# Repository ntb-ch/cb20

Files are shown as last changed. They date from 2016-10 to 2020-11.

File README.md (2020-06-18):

# cb20
Controller Board with Processor Module Toradex Colibri iMX6

## Documentation
- Hardware and software: https://wiki.ntb.ch/infoportal/embedded_systems/imx6/cb
- Linux on the cb20: https://wiki.ntb.ch/infoportal/software/linux/toradex/start

## FPGA Designs
There are currently three FPGA designs in the repository:
* standard: design with encoder inputs, DAC, PWM outputs and some digital I/O pins
* watchdog: similar to standard design, adds PPWA and watchdog with fewer PWM pins
* mpu9250: similar to standard design, adds SPI interface for the MPU-9250 IMU chip of InvenSense, with fewer PWM channels

## Software
We use the board together with [EEROS Robotics Framework](https://github.com/eeros-project/eeros-framework) and [flink](https://github.com/flink-project).
- Demo application: in this repository under Software/cb20test
- How to use, see [Get Started Using EEROS](https://wiki.eeros.org/getting_started/start)

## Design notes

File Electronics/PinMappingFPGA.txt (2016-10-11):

PIN-Mapping FPGA:

=== IO ===
IO_1:	P1\\
IO_2:	P2\\
IO_3:	N1\\
IO_4:	N2\\
IO_5:	L1\\
IO_6:	L2\\
IO_7:	K1\\
IO_8:	K2\\

=== PWM ===
PWM_1:	A2\\
PWM_2:	B3\\
PWM_3:	A3\\
PWM_4:	B4\\
PWM_5:	A4\\
PWM_6:	B5\\
PWM_7:	A5\\
PWM_8:	A6\\

=== Enable/Ready ===
ENABLE:			G1\\
READY_DRV_1:	G2\\
READY_DRV_2:	F1\\
READY_DRV_3:	F2\\
READY_DRV_4:	D1\\
READY_DRV_5:	D2\\
READY_DRV_6:	C1\\
READY_DRV_7:	C2\\
READY_DRV_8:	B1\\

=== Encoder ===
ENC_A1:	L8\\
ENC_B1:	M8\\
ENC_A2:	T5\\
ENC_B2: R4\\
ENC_A3:	T4\\
ENC_B3:	R3\\
ENC_A4:	T3\\
ENC_B4:	T2\\
ENC_A5:	P6\\
ENC_B5:	P3\\
ENC_A6:	N3\\
ENC_B6: N5\\
ENC_A7: N6\\
ENC_B7:	M6\\
ENC_A8:	M7\\
ENC_B8:	L7\\

=== SPI DAC ===
!CLR:	R5\\
!SYNC:	T6\\
!LDAC:	R6\\
MOSI:	T7\\
SCLK:	R7\\

=== EIM ===
DATA0:	T15\\
DATA1:	P14\\
DATA2:	R14\\
DATA3:	T14\\
DATA4:	R13\\
DATA5:	T13\\
DATA6:	N12\\
DATA7:	R12\\
DATA8:	T12\\
DATA9:	N11\\
DATA10:	P11\\
DATA11:	R11\\
DATA12:	T11\\
DATA13:	R10\\
DATA14:	T10\\
DATA15:	P9\\

ADDRESS0:	J15\\
ADDRESS1:	J16\\
ADDRESS2:	J13\\
ADDRESS3:	J14\\
ADDRESS4:	L13\\
ADDRESS5:	L14\\
ADDRESS6:	N15\\
ADDRESS7:	N16\\
ADDRESS8:	K16\\
ADDRESS9:	K15\\
ADDRESS10:	N14\\
ADDRESS11:	P16\\
ADDRESS12:	P15\\
ADDRESS13:	R16\\
ADDRESS14:	L15\\
ADDRESS15:	L16\\

CS1:		G16\\
CS0:		G15\\
OE:		F13\\
PWE:		F16\\
RDY:		F15\\
DF_WE:		B16\\
RD_WR:		F14\\
WE:		D16\\
BE0:		D15\\
BE1:		C16\\
DF_RE_OE:	C15\\

=== Config ===
DCLK:		H1\\
CONF_DONE:	H14\\
nCONFIG:	H5\\
nSTATUS:	F4\\

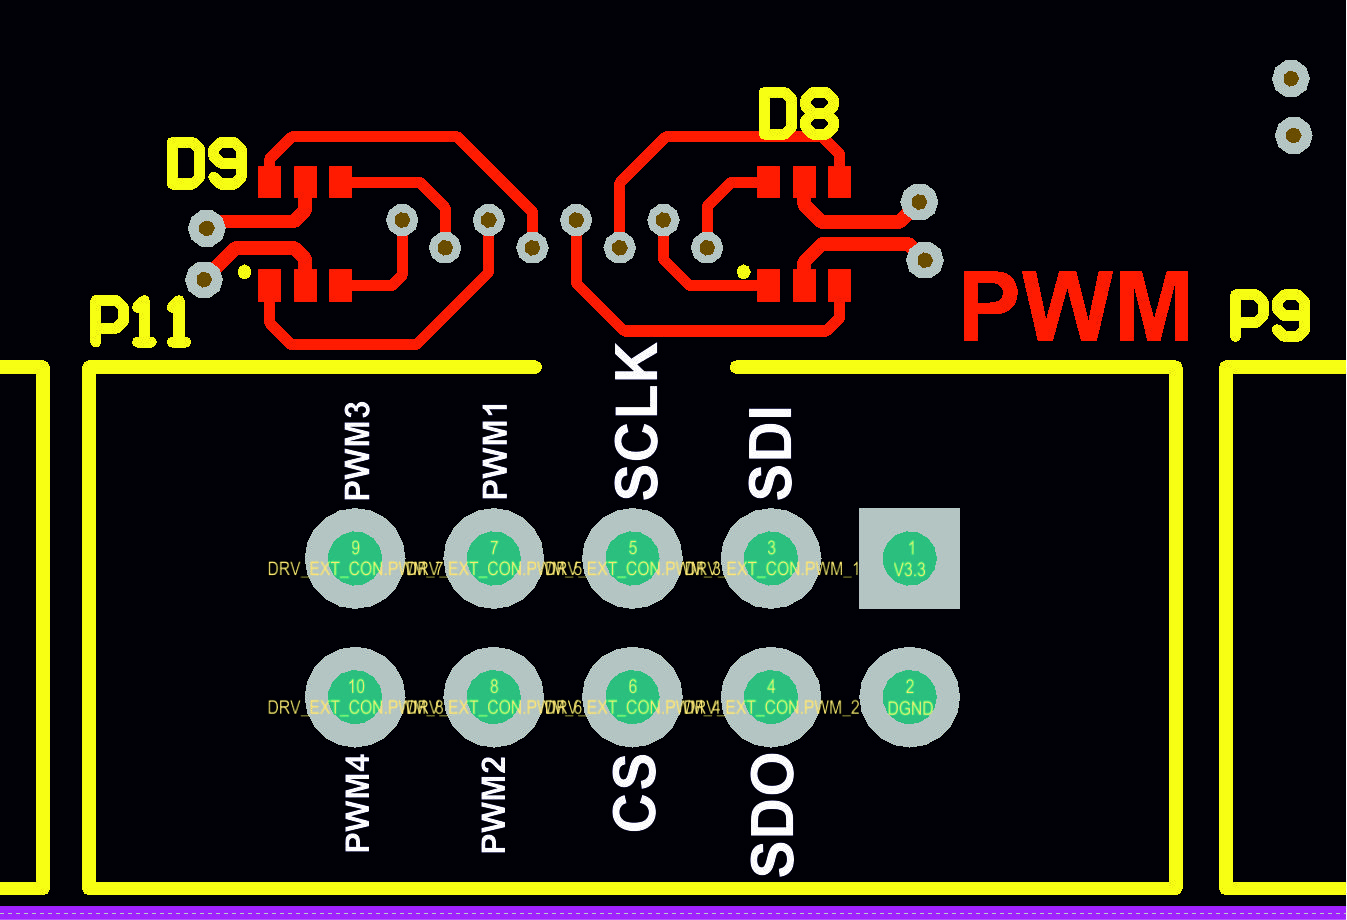
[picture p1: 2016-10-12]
Electronics/Cb20Spi.jpg

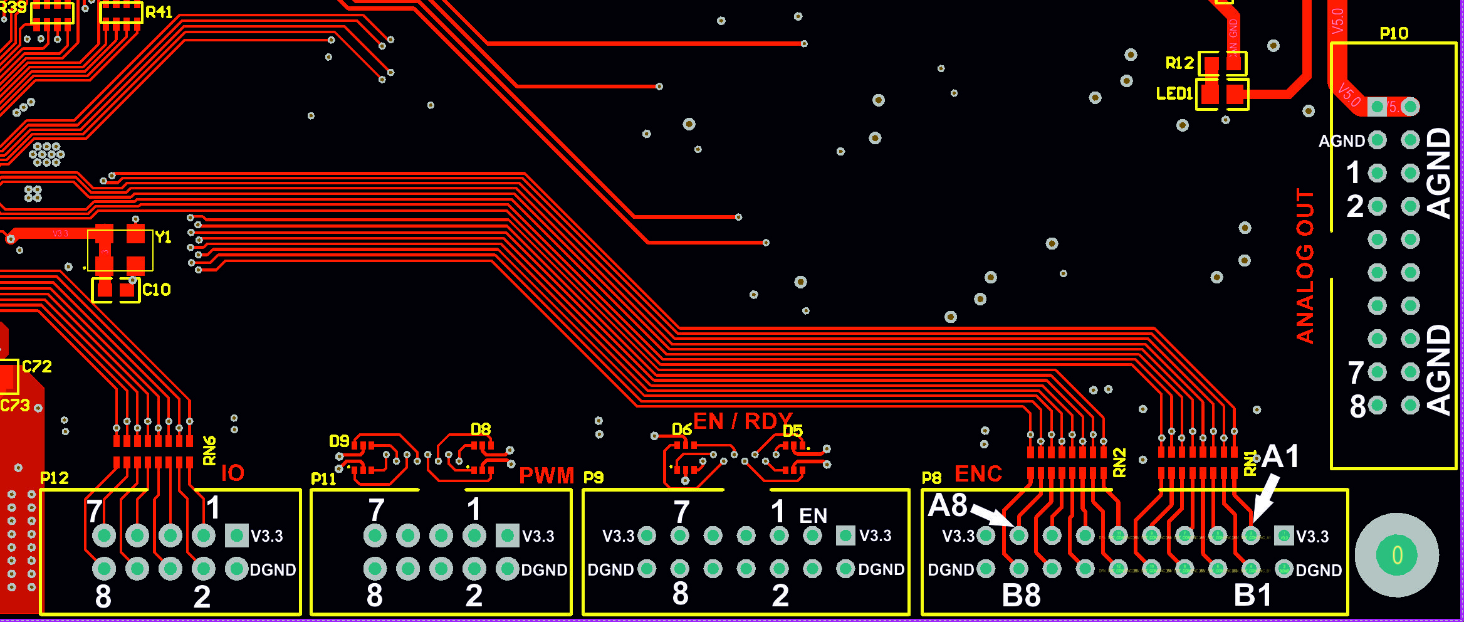
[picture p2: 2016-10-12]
Electronics/PinMappingCb20.jpg

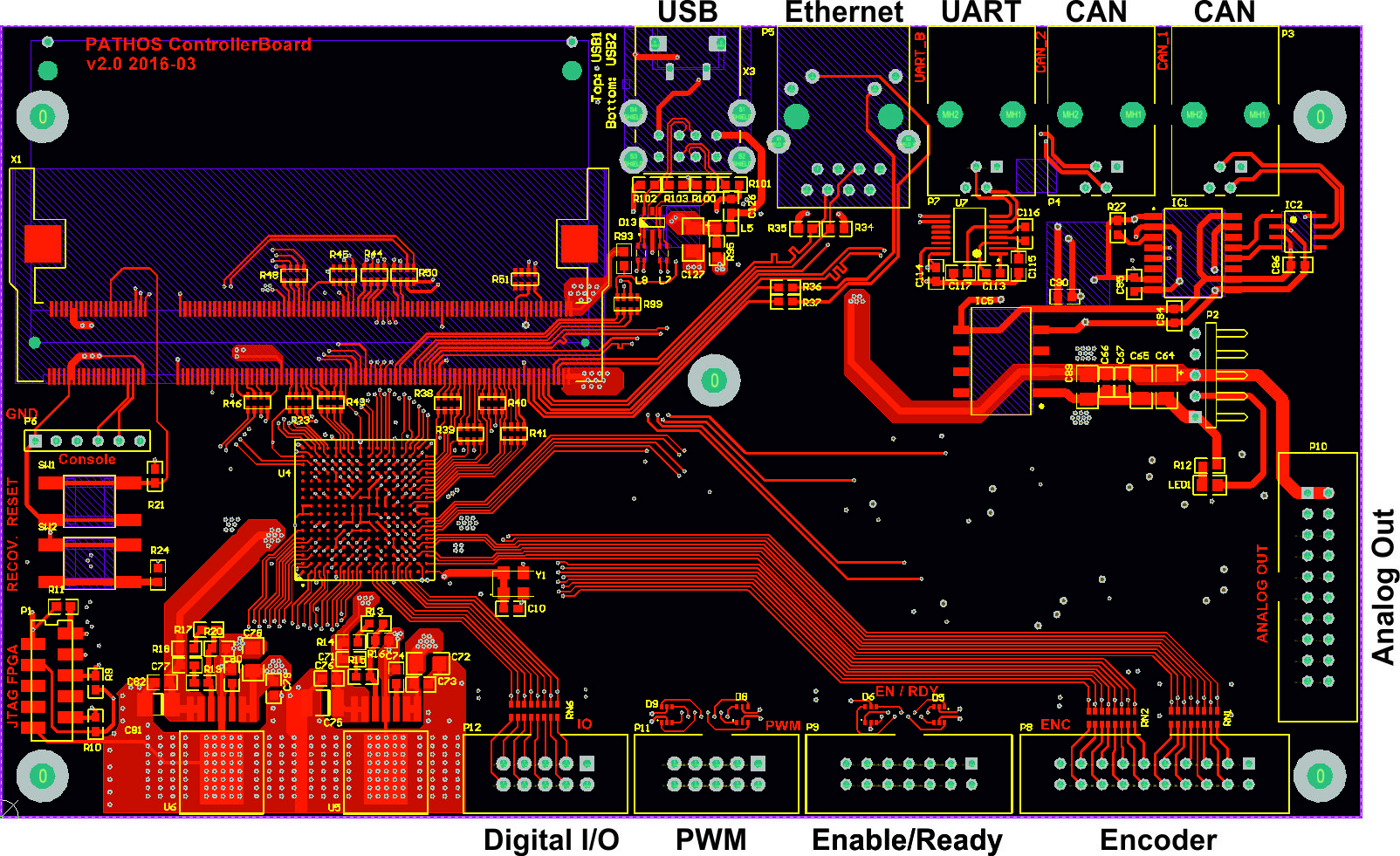
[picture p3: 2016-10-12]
Electronics/Cb20Layout.jpg

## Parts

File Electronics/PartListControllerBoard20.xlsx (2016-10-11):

PATHOS: Bill of Materials Controller Board
 | Farnell (www.farnell.ch)
 | Quantity | Designator | Order Number | Description | minimum Order Quantity | Price | Price/Board | Remarks
 | 1 | (P1) | 149081 | Micro-Match 10pin, Stecker Flachbandkabelanschluss | ab 10Stk. | 1.66 | 1.66 | Not mounted (counterpart to P1)
 | 1 | (P2) | 1462874 | Molex 22-01-3057 KK 2695, 5 Pol Buchsengehäuse |  | 0.1745 | 0.1745 | Not mounted (counterpart to P4)
 | 5 | (P2) | 2424111 | Molex Crimpcontact 08-50-0032 Baureihe 4809 | min. 100Stk. | 0.0641 | 0.3205 | Not mounted (needs 5 crimpcontacts per counterpart of header P4)
 | 3 | (P3, P4, P7) | 1125135 | RJ10 Molex 4P4C 90075-0027 Crimp |  | 0.805 | 2.415 | Not mounted (counterpart to P3, P4, P7)
 | 36 | C1, C8, C10, C67, C83, C84, C85, C86, C87, C88, C91, C92, C93, C99, C100, C101, C102, C103, C104, C105, C113, C114, C115, C116, C117, C118, C119, C120, C121, C122, C123, C124, C125, C126, C128 | 1759123 | Capacitor 100nF 0603, 50V | min. 100Stk. | 0.0109 | 0.3924
 | 2 | C13, C14 | 1740585 | Capacitor 2.2nF, 0402, 50V | ab 10Stk. | 0.146 | 0.292
 | 2 | C15, C16 | 1327656 | Capacitor 4.7nF, 0402, 50V | ab 10Stk. | 0.0445 | 0.089
 | 18 | C17, C18, C39, C40, C41, C42, C43, C44, C45, C46, C56, C57, C58, C59, C60, C61, C62, C63 | 1828887 | Capacitor 10nF, 50V, 0402 | 100Stk. Voraussichtlich | 0.0135 | 0.243
 | 2 | C19, C20 | 2211183 | Capacitor 470nF, 50V, 0603 | ab 10Stk. | 0.129 | 0.258
 | 10 | C2, C6, C66, C106, C107, C108, C109, C110, C111, C112 | 1650831 | Capacitor 10nF 0603, 50V | 100 Stk. voraussichtlich | 0.0146 | 0.146
 | 24 | C21, C22, C23, C24, C25, C26, C27, C28, C31, C32, C33, C34, C35, C36, C37, C38, C47, C48, C49, C50, C52, C53, C54, C55 | 2218856 | Capacitor 100nF, 50V, 0402 | ab 50 Stk. | 0.0978 | 2.3472
 | 2 | C3, C51 | 2309028 | Capacitor 10uF, 10V, 0603 |  | 0.471 | 0.942
 | 5 | C4, C73, C76, C79, C82 | 1759116 | Capacitor 47nF, 50V, 0603 | ab 10Stk. | 0.0179 | 0.0895
 | 2 | C5, C90 | 1658868 | Capacitor 1uF, 25V, 0603 | min. 10 Stk. | 0.518 | 1.036
 | 4 | C64, C68, C127, C129 | 2425587 | Capacitor 100uF, 6.3V, 1206 |  | 1.1 | 4.4
 | 3 | C7, C78, C89 | 1735545 | Capacitor 4.7uF, 50V, 1206 | min. 10Stk.; Preis 10Stk. 6.46 | 0.646 | 1.938
 | 1 | C71 | 498580 | Capacitor 470pF, 50V, 0603 | ab 10Stk. | 0.0406 | 0.0406
 | 2 | C74, C80 | 2210853 | Capacitor 2.7nF, 50V, 0603 | ab 10Stk. | 0.1903 | 0.3806
 | 1 | C75 | 1843162 | Capacitor 100uF, 6.3V, 1812 |  | 2.25 | 2.25
 | 1 | C77 | 317202 | Capacitor 1nF, 0603, 50V | ab 10Stk. | 0.0411 | 0.0411
 | 1 | C81 | 2354855 | Capacitor 220uF 2R5TPE220MAFB, 2.5V, 3528 |  | 0.821 | 0.821
 | 6 | L1, L2, L3, L4, L5, L6 | 1515716 | EMI Filter 0603 BLM18EG221SN1D, 220Ohm, 2A | min. 5 Stk. | 0.1154 | 0.6924
 | 1 | L9 | 1515742 | EMI BLM18PG330SN1D 0603, 33Ohm@100MHz, 3A | min. 10Stk. | 0.0573 | 0.0573
 | 1 | P1 | 2452476 | Micro-Match 10pin, Buchse SMD | ab 10Stk. | 2.09 | 2.09 | Not mounted
 | 2 | P11, P12 | 1642019 | Wire-To-Board Header 10Pol WURT 61201021621 | ab 10Stk. 0.562 | 0.589 | 1.178
 | 1 | P2 | 9731636 | Molex Wire-To-Board Header 22-05-7058, 90° angled | min. 10Stk.; Preis 10Stk. 6.46 | 0.0111 | 0.0111
 | 3 | P3, P4, P7 | 2076090 | RJ10 Molex 4P4C Buchse Printmontage | ab 10Stk. | 1.55 | 4.65
 | 1 | P6 | 1248144 | Board-to-Board Header 6 Pin, 1 Row | min. 10Stk. | 0.305 | 0.305
 | 2 | P8, P10 | 1642021 | Wire-To-Board Header 20Pol WURTH 61202021621 | ab 10Stk. 1.1 | 1.2 | 2.4
 | 1 | P9 | 2356253 | Wire-To-Board Header 14Pol WURTH 61201421621 | ab 10Stk. 1.15 | 1.85 | 1.85
 | 3 | R11, R14, R98 | 9331697 | Resistor 1kOhm, 50V, 0603 | ab 10Stk. | 0.0113 | 0.0339
 | 2 | R12, R97 | 9332200 | Resistor 560 Ohm, 50V, 0603 | ab 10Stk. | 0.0115 | 0.023 | R97 not mounted
 | 1 | R13 | 9331034 | Resistor 33kOhm, 0603, 50V | ab 10Stk. | 0.014 | 0.014
 | 1 | R15 | 1795293 | Resistor 12kOhm, 0603, 50V |  | 0.01 | 0.01
 | 1 | R16 | 2138433 | Resistor 16kOhm, 0603, 75V | ab 10Stk. | 0.0114 | 0.0114
 | 1 | R17 | 9330771 | Resistor 20kOhm, 0603, 50V | ab 10Stk. | 0.014 | 0.014
 | 1 | R19 | 1653122 | Resistor 3.3kOhm, 0603 | ab 10Stk. | 0.0471 | 0.0471
 | 36 | R2, R3, R4, R5, R6, R7, R8, R9, R10, R24, R52, R53, R56, R57, R58, R59, R62, R63, R66, R67, R68, R69, R72, R73, R76, R77, R78, R79, R82, R83, R86, R87, R88, R89, R93, R94 | 2335831 | Resistor 10KOhm, 0603 | ab 50Stk. | 0.0678 | 2.4408
 | 1 | R20 | 9331204 | Resistor 43kOhm, 0603, 50V | ab 10Stk. | 0.014 | 0.014
 | 4 | R21, R22, R27, R30 | 9331719 | Resistor 100kOhm, 50V, 0603 | ab 10Stk. | 0.0109 | 0.0436
 | 16 | R23, R38, R39, R40, R41, R42, R43, R44, R45, R46, R47, R48, R49, R50, R51, R99 | 1770118 | Resistor Array CAT16-220J4LF 22Ohm |  | 0.167 | 2.672
 | 11 | R25, R26, R28, R29, R31, R92, R95, R96, R104, R105, R106 | 9331662 | Resistor 0Ohm, 50V, 0603 | ab 10Stk. | 0.0111 | 0.1221 | R25, R28, R95, R96, R104, R105, R106 not mounted
 | 4 | R32, R33, R34, R35 | 2112878 | Resistor 50Ohm, 0603 | ab 50Stk. | 0.0364 | 0.1456
 | 2 | R36, R37 | 1527376 | Resistor 150Ohm, 0603 |  | 0.0933 | 0.1866
 | 12 | R54, R55, R64, R65, R74, R75, R84, R85, R100, R101, R102, R103 | 9330615 | Resistor 15kOhm, 0603, 50V | ab 10Stk. | 0.014 | 0.168
 | 8 | R60, R61, R70, R71, R80, R81, R90, R91 | 1652854 | Resistor 1.8kOhm, 0603, 75V | ab 10Stk. | 0.0148 | 0.1184
 | 2 | SW1, SW2 | 1555991 | Micro Miniature Push-Button FSM6JSMA SMD | min. 25Stk. | 0.624 | 1.248 | SW2 not mounted
 | 2 | U5, U6 | 2102677 | LMZ10503TZE-ADJ/NOPB, Buck Regulator |  | 8.7 | 17.4
 | Mouser (www.mouser.com)
 | Quantity | Designator | Order Number | Description | minimum Order Quantity | Price |  | Remarks
 | 6 | C11, C12, C29, C30, C94, C95 | 810-C2012X5R1A476M | Capacitor 47uF, 0805, 10V | ab 10Stk. | 0.749 | 4.494
 | 4 | C65, C69, C70, C72 | 81-GRM31CR61H106KA2L | Capacitor 10uF, 50V, 1206 | min. 10 Stk, ca. 20 bestellen | 0.408 | 1.632
 | 3 | C96, C97, C98 | 80-A700X157M6E15 | Capacitor 150uF A700X157M006ATE015, 6V Tantal | ab 10Stk. | 3.29 | 9.87
 | 11 | D1, D2, D3, D4, D5, D6, D7, D8, D9, D10, D11 | 621-QSBT40-F | Schottky Dioden & Gleichrichter 30V 200mW, QSBT40-7-F |  | 0.71 | 7.81
 | 1 | D12 | 595-TPD2EUSB30DRTR | ESD Protector TPD2EUSB30DRTR | ab 10Stk. 0.46 | 0.548 | 0.548 | Not mounted
 | 1 | D13 | 947-RCLAMP0504S.TCT | TVS Suppressor RCLAMP0504S.TCT | ab 10Stk. 0.846 | 1.05 | 1.05
 | 2 | IC1, IC3 | 584-ADUM1301ARW | Digital Isolator ADUM1301ARW |  | 4.72 | 9.44
 | 2 | IC2, IC4 | 579-MCP2551T-I/SN | CAN-IC-Schnittstelle Hi Spd CAN Transceiver MCP2551T |  | 1.09 | 2.18
 | 1 | IC5 | 580-NTE0505MC-R | DC-DC Converter 5V, NTE0505MC |  | 8.56 | 8.56
 | 1 | IC6 | 595-TPS2042BDR | USB Current Limit Power Switch TPS2042BDR | ab 10Stk. 1.47 | 1.74 | 1.74
 | 2 | L7, L8 | 81-DLW21HN900SQ2L | Common Mode Choke, 90Ohm@100MHz, 330mA | ab 10Stk. 0.375 | 0.518 | 1.036
 | 1 | LED1 | 720-LGR971-KN-1 | LED green, 20mA, 0805 | ab 10Stk. | 0.064 | 0.064
 | 1 | P5 | 673-J00-0065NL | RJ45 Header J00-0065NL |  | 5.84 | 5.84
 | 1 | R1 | 71-CRCW0603J-1.2K-E3 | Resistor 1.2kOhm, 0603, 75V |  | 0.098 | 0.098
 | 1 | R18 | 71-CRCW0603-1.5K-E3 | Resistor 1.5kOhm, 0603, 75V |  | 0.098 | 0.098
 | 6 | RN1, RN2, RN3, RN4, RN5, RN6 | 774-742C163470JP | Resistor-Array 47Ohm, 50V, 5% | ab 10Stk. Min. 3 Stk. | 0.355 | 2.13
 | 1 | U1 | 584-AD5668BRUZ-1 | Digital-in-Analog-Wandler - DAC AD5668BRUZ-1 Octal 16-bit 8CH SPI |  | 22.9 | 22.9
 | 1 | U2 | 584-AD1582ARTZ-R2 | Spannungsreferenzen 25V MICROPOWER REF IC |  | 2.09 | 2.09
 | 1 | U3 | 584-ADR1581BRTZ-R7 | Spannungsreferenzen 1.25V Micropower Precision Shunt |  | 2.33 | 2.33
 | 1 | U4 | 989-EP4CE22F17C8N | FPGA EP4CE22F17C8N |  | 48.62 | 48.62
 | 1 | U7 | 595-MAX3232CDB | MAX3232CDB |  | 2.73 | 2.73
 | 4 | U8, U9, U10, U11 | 595-TL084CPWR | Operationsverstärker Quad JFET Neg Input |  | 0.507 | 2.028
 | 1 | X1 | 571-1473005-1 | Connector TE 1473005-1, Semi Hard Tray DDR Socket |  | 4.58 | 4.58
 | 1 | X3 | 575-4300890 | USB Type A Connector Mill-Max 896-43-008-90-000000 | ab 10Stk. 2.21 | 2.66 | 2.66 | Add isolation foil/pad between header and PCB to prevent shourtcuts to pads of X4
 | 1 | X4 | 538-47589-0001 | USB-Stecker MICRO USB AB RECPT | ab 10Stk. 0.792 | 0.839 | 0.839 | Not mounted
 | 1 | Y1 | 717-7C-50.000MBA-T | Oscillator 50 MHz, TXC 7C-50.000MBA-T | ab 10 Stk. 2.84 | 3.31 | 3.31
 |  |  |  |  |  | Total/Board: | 206.8997

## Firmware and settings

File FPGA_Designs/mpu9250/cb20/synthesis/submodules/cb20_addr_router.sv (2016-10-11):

// (C) 2001-2013 Altera Corporation. All rights reserved.
// Your use of Altera Corporation's design tools, logic functions and other 
// software and tools, and its AMPP partner logic functions, and any output 
// files any of the foregoing (including device programming or simulation 
// files), and any associated documentation or information are expressly subject 
// to the terms and conditions of the Altera Program License Subscription 
// Agreement, Altera MegaCore Function License Agreement, or other applicable 
// license agreement, including, without limitation, that your use is for the 
// sole purpose of programming logic devices manufactured by Altera and sold by 
// Altera or its authorized distributors.  Please refer to the applicable 
// agreement for further details.


// (C) 2001-2013 Altera Corporation. All rights reserved.
// Your use of Altera Corporation's design tools, logic functions and other 
// software and tools, and its AMPP partner logic functions, and any output 
// files any of the foregoing (including device programming or simulation 
// files), and any associated documentation or information are expressly subject 
// to the terms and conditions of the Altera Program License Subscription 
// Agreement, Altera MegaCore Function License Agreement, or other applicable 
// license agreement, including, without limitation, that your use is for the 
// sole purpose of programming logic devices manufactured by Altera and sold by 
// Altera or its authorized distributors.  Please refer to the applicable 
// agreement for further details.


// $Id: //acds/rel/13.0sp1/ip/merlin/altera_merlin_router/altera_merlin_router.sv.terp#1 $
// $Revision: #1 $
// $Date: 2013/03/07 $
// $Author: swbranch $

// -------------------------------------------------------
// Merlin Router
//
// Asserts the appropriate one-hot encoded channel based on 
// either (a) the address or (b) the dest id. The DECODER_TYPE
// parameter controls this behaviour. 0 means address decoder,
// 1 means dest id decoder.
//
// In the case of (a), it also sets the destination id.
// -------------------------------------------------------

`timescale 1 ns / 1 ns

module cb20_addr_router_default_decode
  #(
     parameter DEFAULT_CHANNEL = 4,
               DEFAULT_WR_CHANNEL = -1,
               DEFAULT_RD_CHANNEL = -1,
               DEFAULT_DESTID = 6 
   )
  (output [59 - 57 : 0] default_destination_id,
   output [7-1 : 0] default_wr_channel,
   output [7-1 : 0] default_rd_channel,
   output [7-1 : 0] default_src_channel
  );

  assign default_destination_id = 
    DEFAULT_DESTID[59 - 57 : 0];

  generate begin : default_decode
    if (DEFAULT_CHANNEL == -1) begin
      assign default_src_channel = '0;
    end
    else begin
      assign default_src_channel = 7'b1 << DEFAULT_CHANNEL;
    end
  end
  endgenerate

  generate begin : default_decode_rw
    if (DEFAULT_RD_CHANNEL == -1) begin
      assign default_wr_channel = '0;
      assign default_rd_channel = '0;
    end
    else begin
      assign default_wr_channel = 7'b1 << DEFAULT_WR_CHANNEL;
      assign default_rd_channel = 7'b1 << DEFAULT_RD_CHANNEL;
    end
  end
  endgenerate

endmodule


module cb20_addr_router
(
    // -------------------
    // Clock & Reset
    // -------------------
    input clk,
    input reset,

    // -------------------
    // Command Sink (Input)
    // -------------------
    input                       sink_valid,
    input  [70-1 : 0]    sink_data,
    input                       sink_startofpacket,
    input                       sink_endofpacket,
    output                      sink_ready,

    // -------------------
    // Command Source (Output)
    // -------------------
    output                          src_valid,
    output reg [70-1    : 0] src_data,
    output reg [7-1 : 0] src_channel,
    output                          src_startofpacket,
    output                          src_endofpacket,
    input                           src_ready
);

    // -------------------------------------------------------
    // Local parameters and variables
    // -------------------------------------------------------
    localparam PKT_ADDR_H = 34;
    localparam PKT_ADDR_L = 18;
    localparam PKT_DEST_ID_H = 59;
    localparam PKT_DEST_ID_L = 57;
    localparam PKT_PROTECTION_H = 63;
    localparam PKT_PROTECTION_L = 61;
    localparam ST_DATA_W = 70;
    localparam ST_CHANNEL_W = 7;
    localparam DECODER_TYPE = 0;

    localparam PKT_TRANS_WRITE = 37;
    localparam PKT_TRANS_READ  = 38;

    localparam PKT_ADDR_W = PKT_ADDR_H-PKT_ADDR_L + 1;
    localparam PKT_DEST_ID_W = PKT_DEST_ID_H-PKT_DEST_ID_L + 1;



    // -------------------------------------------------------
    // Figure out the number of bits to mask off for each slave span
    // during address decoding
    // -------------------------------------------------------
    localparam PAD0 = log2ceil(64'h100 - 64'h0); 
    localparam PAD1 = log2ceil(64'h180 - 64'h100); 
    localparam PAD2 = log2ceil(64'h200 - 64'h180); 
    localparam PAD3 = log2ceil(64'h280 - 64'h200); 
    localparam PAD4 = log2ceil(64'h300 - 64'h280); 
    localparam PAD5 = log2ceil(64'h340 - 64'h300); 
    localparam PAD6 = log2ceil(64'h380 - 64'h340); 
    // -------------------------------------------------------
    // Work out which address bits are significant based on the
    // address range of the slaves. If the required width is too
    // large or too small, we use the address field width instead.
    // -------------------------------------------------------
    localparam ADDR_RANGE = 64'h380;
    localparam RANGE_ADDR_WIDTH = log2ceil(ADDR_RANGE);
    localparam OPTIMIZED_ADDR_H = (RANGE_ADDR_WIDTH > PKT_ADDR_W) ||
                                  (RANGE_ADDR_WIDTH == 0) ?
                                        PKT_ADDR_H :
                                        PKT_ADDR_L + RANGE_ADDR_WIDTH - 1;

    localparam RG = RANGE_ADDR_WIDTH-1;

      wire [PKT_ADDR_W-1 : 0] address = sink_data[OPTIMIZED_ADDR_H : PKT_ADDR_L];

    // -------------------------------------------------------
    // Pass almost everything through, untouched
    // -------------------------------------------------------
    assign sink_ready        = src_ready;
    assign src_valid         = sink_valid;
    assign src_startofpacket = sink_startofpacket;
    assign src_endofpacket   = sink_endofpacket;

    wire [PKT_DEST_ID_W-1:0] default_destid;
    wire [7-1 : 0] default_src_channel;





    cb20_addr_router_default_decode the_default_decode(
      .default_destination_id (default_destid),
      .default_wr_channel   (),
      .default_rd_channel   (),
      .default_src_channel  (default_src_channel)
    );

    always @* begin
        src_data    = sink_data;
        src_channel = default_src_channel;
        src_data[PKT_DEST_ID_H:PKT_DEST_ID_L] = default_destid;
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

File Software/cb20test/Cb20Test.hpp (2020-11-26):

#ifndef CB20_TEST_HPP_
#define CB20_TEST_HPP_

#include <eeros/control/PeripheralOutput.hpp>
#include <eeros/control/PeripheralInput.hpp>
#include <eeros/control/Constant.hpp>
#include <eeros/control/TimeDomain.hpp>
#include <eeros/hal/HAL.hpp>
#include <eeros/core/Executor.hpp>
#include <eeros/sequencer/Sequence.hpp>
#include <eeros/sequencer/Sequencer.hpp>
#include <unistd.h>

using namespace eeros::safety;
using namespace eeros::control;
using namespace eeros::sequencer;
using namespace eeros::hal;

const double dt = 0.001;

class TestSafetyProperties : public SafetyProperties {
public:
	TestSafetyProperties() : slSingle("single level") {
		addLevel(slSingle);
		setEntryLevel(slSingle);
	}
	SafetyLevel slSingle;
};

class MainSequence : public Sequence {
public:
	MainSequence(Sequencer& sequencer) : Sequence("main", sequencer) {
		hal.callOutputFeature(&pwm1, "setPwmFrequency", 100.0);
		hal.callOutputFeature(&pwm2, "setPwmFrequency", 100.0);
		hal.callOutputFeature(&pwm3, "setPwmFrequency", 100.0);
		hal.callOutputFeature(&pwm4, "setPwmFrequency", 100.0);
		hal.callOutputFeature(&pwm5, "setPwmFrequency", 100.0);
		hal.callOutputFeature(&pwm6, "setPwmFrequency", 100.0);
		hal.callOutputFeature(&pwm7, "setPwmFrequency", 100.0);
		hal.callOutputFeature(&pwm8, "setPwmFrequency", 100.0);
		dac1.set(0);
		dac2.set(0);
		dac3.set(0);
		dac4.set(0);
		dac5.set(0);
		dac6.set(0);
		dac7.set(0);
		dac8.set(0);
	}
	
	int action() {
		int cnt = 0;
		pwm1.set(0.1);	// check pwm duty cycles on P11, pins 3 through to 10
		pwm2.set(0.2);
		pwm3.set(0.3);
		pwm4.set(0.4);
		pwm5.set(0.5);
		pwm6.set(0.6);
		pwm7.set(0.7);
		pwm8.set(0.8);
		
		while (Sequencer::running) {
			if(cnt%10 == 0){
				// GPIO
				io1.set(!io1.get());	// check on P12, pin 3, must toggle with 5Hz
				io4.set(!io4.get());	// check on P12, pin 6, must toggle with 5Hz
				io7.set(!io7.get());	// check on P12, pin 9, must toggle with 5Hz
				enableDrv.set(!enableDrv.get());	// check on P9, pin 3, must toggle with 5Hz
				readySig3.set(!readySig3.get());	// check on P9, pin 7, must toggle with 5Hz
				readySig6.set(!readySig6.get());	// check on P9, pin 10, must toggle with 5Hz
			}
			if(cnt%15 == 0){
				io2.set(!io2.get());	// check on P12, pin 4, must toggle with 3.3Hz
				io5.set(!io5.get());	// check on P12, pin 7, must toggle with 3.3Hz
				io8.set(!io8.get());	// check on P12, pin 10, must toggle with 3.3Hz
				readySig1.set(!readySig1.get());	// check on P9, pin 5, must toggle with 3.3Hz
				readySig4.set(!readySig4.get());	// check on P9, pin 8, must toggle with 3.3Hz
				readySig7.set(!readySig7.get());	// check on P9, pin 11, must toggle with 3.3Hz
			}
			if(cnt%20 == 0){
				io3.set(!io3.get());	// check on P12, pin 5, must toggle with 2.5Hz
				io6.set(!io6.get());	// check on P12, pin 8, must toggle with 2.5Hz
				readySig2.set(!readySig2.get());	// check on P9, pin 6, must toggle with 2.5Hz
				readySig5.set(!readySig5.get());	// check on P9, pin 9, must toggle with 2.5Hz
				readySig8.set(!readySig8.get());	// check on P9, pin 12, must toggle with 2.5Hz
			}
			if(cnt%100 == 0){	// connect encoders to P8
				log.info() << enc1.get() << "\t" << enc2.get() << "\t"
				<< enc3.get() << "\t" << enc4.get() << "\t" << enc5.get() << "\t" 
				<< enc6.get() << "\t" << enc7.get() << "\t" << enc8.get();
			}
			
			if((dac1val+=0.5) > 10.0) dac1val = -10.0;	// check analog signals (ramp) on P10
			dac1.set(dac1val);
			if((dac2val+=1.0) > 10.0) dac2val = -10.0;
			dac2.set(dac2val);
			if((dac3val+=0.4) > 10.0) dac3val = -10.0;
			dac3.set(dac3val);
			if((dac4val+=0.8) > 10.0) dac4val = -10.0;
			dac4.set(dac4val);
			if((dac5val+=0.5) > 10.0) dac5val = -10.0;
			dac5.set(dac5val);
			if((dac6val+=0.2) > 10.0) dac6val = -10.0;
			dac6.set(dac6val);
			if((dac7val+=0.6) > 10.0) dac7val = -10.0;
			dac7.set(dac7val);
			if((dac8val+= 0.8) > 10.0) dac8val = -10.0;
			dac8.set(dac8val);
			
			cnt++;
			usleep(10000);
		}
	}
	
private:
	HAL& hal = HAL::instance();
	eeros::hal::Output<bool>& io1 = *hal.getLogicOutput("io1");
	eeros::hal::Output<bool>& io2 = *hal.getLogicOutput("io2");
	eeros::hal::Output<bool>& io3 = *hal.getLogicOutput("io3");
	eeros::hal::Output<bool>& io4 = *hal.getLogicOutput("io4");
	eeros::hal::Output<bool>& io5 = *hal.getLogicOutput("io5");
	eeros::hal::Output<bool>& io6 = *hal.getLogicOutput("io6");
	eeros::hal::Output<bool>& io7 = *hal.getLogicOutput("io7");
	eeros::hal::Output<bool>& io8 = *hal.getLogicOutput("io8");
	eeros::hal::Output<double>& pwm1 = *hal.getScalableOutput("pwm1");
	eeros::hal::Output<double>& pwm2 = *hal.getScalableOutput("pwm2");
	eeros::hal::Output<double>& pwm3 = *hal.getScalableOutput("pwm3");
	eeros::hal::Output<double>& pwm4 = *hal.getScalableOutput("pwm4");
	eeros::hal::Output<double>& pwm5 = *hal.getScalableOutput("pwm5");
	eeros::hal::Output<double>& pwm6 = *hal.getScalableOutput("pwm6");
	eeros::hal::Output<double>& pwm7 = *hal.getScalableOutput("pwm7");
	eeros::hal::Output<double>& pwm8 = *hal.getScalableOutput("pwm8");
	eeros::hal::Output<double>& dac1 = *hal.getScalableOutput("dac1");
	eeros::hal::Output<double>& dac2 = *hal.getScalableOutput("dac2");
	eeros::hal::Output<double>& dac3 = *hal.getScalableOutput("dac3");
	eeros::hal::Output<double>& dac4 = *hal.getScalableOutput("dac4");
	eeros::hal::Output<double>& dac5 = *hal.getScalableOutput("dac5");
	eeros::hal::Output<double>& dac6 = *hal.getScalableOutput("dac6");
	eeros::hal::Output<double>& dac7 = *hal.getScalableOutput("dac7");
	eeros::hal::Output<double>& dac8 = *hal.getScalableOutput("dac8");
	eeros::hal::Output<bool>& enableDrv = *hal.getLogicOutput("enableDrv");
	// the ready signals are inputs when connected to drives
	// for testing purposes we configure them as outputs 
	eeros::hal::Output<bool>& readySig1 = *hal.getLogicOutput("readySig1");
	eeros::hal::Output<bool>& readySig2 = *hal.getLogicOutput("readySig2");
	eeros::hal::Output<bool>& readySig3 = *hal.getLogicOutput("readySig3");
	eeros::hal::Output<bool>& readySig4 = *hal.getLogicOutput("readySig4");
	eeros::hal::Output<bool>& readySig5 = *hal.getLogicOutput("readySig5");
	eeros::hal::Output<bool>& readySig6 = *hal.getLogicOutput("readySig6");
	eeros::hal::Output<bool>& readySig7 = *hal.getLogicOutput("readySig7");
	eeros::hal::Output<bool>& readySig8 = *hal.getLogicOutput("readySig8");
	eeros::hal::Input<double>& enc1 = *hal.getScalableInput("enc1");
	eeros::hal::Input<double>& enc2 = *hal.getScalableInput("enc2");
	eeros::hal::Input<double>& enc3 = *hal.getScalableInput("enc3");
	eeros::hal::Input<double>& enc4 = *hal.getScalableInput("enc4");
	eeros::hal::Input<double>& enc5 = *hal.getScalableInput("enc5");
	eeros::hal::Input<double>& enc6 = *hal.getScalableInput("enc6");
	eeros::hal::Input<double>& enc7 = *hal.getScalableInput("enc7");
	eeros::hal::Input<double>& enc8 = *hal.getScalableInput("enc8");
	double dac1val = 0.0;
	double dac2val = 0.0;
	double dac3val = 0.0;
	double dac4val = 0.0;
	double dac5val = 0.0;
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

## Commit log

2016-10-11 files electronics added
    [PATHOS_AnalogOut.SchDoc, PATHOS_AnalogOutLevelShifter.SchDoc, PATHOS_ControllerBoardExp.PrjPCB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]
2016-10-12 pin mapping images added
2016-10-12 fix fpga design, add pwm pin on empty pin
2017-01-10 rename of altium files
    [AnalogOut.SchDoc, AnalogOutLevelShifter.SchDoc, ControllerBoardExp.PrjPCB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]
2017-05-04 Update config.sh.in
    enable toolchain file for arm
2017-06-07 rootfsOverlay and users file added for buildroot
    [config.txt, configsystem.txt]
2017-06-30 test for drive board added
2020-06-18 Delete files for previous root file system
    We changed to Yocto build with integrated SDK.
    [config.txt, configsystem.txt]
